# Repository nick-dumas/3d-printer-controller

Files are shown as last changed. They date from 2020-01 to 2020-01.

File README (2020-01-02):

This project is a 3D printer controller board.

The goals are (in the following order):
 * Safety (No electrical/fire hazards)
 * Print quality on par with the Duet
 * Modularity on par with ramps
 * Hobbiest level assembly difficulty
 * Cheap

It is intended to be used with a 24v LED strip switching PSU, as well as an external 5v buck-boost regulator.

Currently licensed under:
 Creative Commons Attribution-NonCommercial-ShareAlike 4.0 International License
 http://creativecommons.org/licenses/by-nc-sa/4.0/

This means share-alike, non-commercial.
I plan to release this under a open MIT license once the project is built and complete.
I would also appreciate if you let me know if and how you are using this project.

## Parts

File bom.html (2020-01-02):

Ref | Qnty | Value | Part | Footprint | Description | Vendor
A1, A2, A3, A4 | 4 | A9488_BREAKOUT | 3d-printer-controller:Pololu_Breakout_A4988 | Module:Pololu_Breakout-16_15.2x20.3mm | Pololu Breakout Board, Stepper Driver A4988
C1, C2, C4, C6, C7, C8, C9 | 7 | 1u | 3d-printer-controller:C | Capacitor_THT:C_Disc_D7.5mm_W2.5mm_P5.00mm | Unpolarized capacitor
C3, C5, C14, C15 | 4 | 10u | 3d-printer-controller:CP | Capacitor_THT:CP_Radial_D8.0mm_P5.00mm | Polarized capacitor
C10, C11, C12, C13 | 4 | 100u | 3d-printer-controller:CP | Capacitor_THT:CP_Radial_D10.0mm_P5.00mm | Polarized capacitor
C16 | 1 | C | 3d-printer-controller:C | Capacitor_THT:CP_Radial_D8.0mm_P5.00mm | Unpolarized capacitor
D1, D2 | 2 | D_Schottky | 3d-printer-controller:D_Schottky | Diode_THT:D_A-405_P10.16mm_Horizontal | Schottky diode
F1 | 1 | FUSE_FAN_1A | 3d-printer-controller:Fuse | Fuse:Fuseholder_Blade_Mini_Keystone_3568 | Fuse
F2 | 1 | FUSE_HEAT_15A | 3d-printer-controller:Fuse | Fuse:Fuseholder_Blade_Mini_Keystone_3568 | Fuse
F3 | 1 | FUSE_MOT_10A | 3d-printer-controller:Fuse | Fuse:Fuseholder_Blade_Mini_Keystone_3568 | Fuse
J1 | 1 | X_MIN | 3d-printer-controller:Conn_01x03 | Connector_PinHeader_2.54mm:PinHeader_1x03_P2.54mm_Vertical | Generic connector, single row, 01x03, script generated (kicad-library-utils/schlib/autogen/connector/)
J2 | 1 | X_MAX | 3d-printer-controller:Conn_01x03 | Connector_PinHeader_2.54mm:PinHeader_1x03_P2.54mm_Vertical | Generic connector, single row, 01x03, script generated (kicad-library-utils/schlib/autogen/connector/)
J3, J5 | 2 | THRM0 | 3d-printer-controller:Conn_01x02 | Connector_PinHeader_2.54mm:PinHeader_2x01_P2.54mm_Vertical | Generic connector, single row, 01x02, script generated (kicad-library-utils/schlib/autogen/connector/)
J4 | 1 | Y_MIN | 3d-printer-controller:Conn_01x03 | Connector_PinHeader_2.54mm:PinHeader_1x03_P2.54mm_Vertical | Generic connector, single row, 01x03, script generated (kicad-library-utils/schlib/autogen/connector/)
J6 | 1 | Y_MAX | 3d-printer-controller:Conn_01x03 | Connector_PinHeader_2.54mm:PinHeader_1x03_P2.54mm_Vertical | Generic connector, single row, 01x03, script generated (kicad-library-utils/schlib/autogen/connector/)
J7 | 1 | Z_MIN | 3d-printer-controller:Conn_01x03 | Connector_PinHeader_2.54mm:PinHeader_1x03_P2.54mm_Vertical | Generic connector, single row, 01x03, script generated (kicad-library-utils/schlib/autogen/connector/)
J8 | 1 | Z_MAX | 3d-printer-controller:Conn_01x03 | Connector_PinHeader_2.54mm:PinHeader_1x03_P2.54mm_Vertical | Generic connector, single row, 01x03, script generated (kicad-library-utils/schlib/autogen/connector/)
J9 | 1 | MICROUSB | 3d-printer-controller:USB_B_Micro | Connector_USB:USB_Micro-B_Molex_47346-0001 | USB Micro Type B connector
J10 | 1 | I2C | 3d-printer-controller:Conn_01x04 | Connector_PinHeader_2.54mm:PinHeader_1x04_P2.54mm_Vertical | Generic connector, single row, 01x04, script generated (kicad-library-utils/schlib/autogen/connector/)
J11 | 1 | SD_Card | 3d-printer-controller:SD_Card | Connector_Card:SD_TE_2041021 | SD Card Reader
J12 | 1 | Z_MOT_JMP | 3d-printer-controller:Conn_02x03_Top_Bottom | Connector_PinHeader_2.54mm:PinHeader_2x03_P2.54mm_Vertical | Generic connector, double row, 02x03, top/bottom pin numbering scheme (row 1: 1...pins_per_row, row2: pins_per_row+1 ... num_pins), script generated (kicad-library-utils/schlib/autogen/connector/)
J13 | 1 | X_MOT_JMP | 3d-printer-controller:Conn_02x03_Top_Bottom | Connector_PinHeader_2.54mm:PinHeader_2x03_P2.54mm_Vertical | Generic connector, double row, 02x03, top/bottom pin numbering scheme (row 1: 1...pins_per_row, row2: pins_per_row+1 ... num_pins), script generated (kicad-library-utils/schlib/autogen/connector/)
J14 | 1 | Z_MOT | 3d-printer-controller:Conn_01x04 | Connector_PinHeader_2.54mm:PinHeader_1x04_P2.54mm_Vertical | Generic connector, single row, 01x04, script generated (kicad-library-utils/schlib/autogen/connector/)
J15 | 1 | X_MOT | 3d-printer-controller:Conn_01x04 | Connector_PinHeader_2.54mm:PinHeader_1x04_P2.54mm_Vertical | Generic connector, single row, 01x04, script generated (kicad-library-utils/schlib/autogen/connector/)
J16 | 1 | E0_MOT_JMP | 3d-printer-controller:Conn_02x03_Top_Bottom | Connector_PinHeader_2.54mm:PinHeader_2x03_P2.54mm_Vertical | Generic connector, double row, 02x03, top/bottom pin numbering scheme (row 1: 1...pins_per_row, row2: pins_per_row+1 ... num_pins), script generated (kicad-library-utils/schlib/autogen/connector/)
J17 | 1 | Y_MOT_JMP | 3d-printer-controller:Conn_02x03_Top_Bottom | Connector_PinHeader_2.54mm:PinHeader_2x03_P2.54mm_Vertical | Generic connector, double row, 02x03, top/bottom pin numbering scheme (row 1: 1...pins_per_row, row2: pins_per_row+1 ... num_pins), script generated (kicad-library-utils/schlib/autogen/connector/)
J18 | 1 | E0_MOT | 3d-printer-controller:Conn_01x04 | Connector_PinHeader_2.54mm:PinHeader_1x04_P2.54mm_Vertical | Generic connector, single row, 01x04, script generated (kicad-library-utils/schlib/autogen/connector/)
J19 | 1 | Y_MOT | 3d-printer-controller:Conn_01x04 | Connector_PinHeader_2.54mm:PinHeader_1x04_P2.54mm_Vertical | Generic connector, single row, 01x04, script generated (kicad-library-utils/schlib/autogen/connector/)
J20 | 1 | FAN1 | 3d-printer-controller:Conn_01x02 | Connector_PinHeader_2.54mm:PinHeader_1x02_P2.54mm_Vertical | Generic connector, single row, 01x02, script generated (kicad-library-utils/schlib/autogen/connector/)
J21 | 1 | FAN0 | 3d-printer-controller:Conn_01x02 | Connector_PinHeader_2.54mm:PinHeader_1x02_P2.54mm_Vertical | Generic connector, single row, 01x02, script generated (kicad-library-utils/schlib/autogen/connector/)
J22 | 1 | HEAT1 | 3d-printer-controller:Conn_01x02 | Connector_PinHeader_2.54mm:PinHeader_1x02_P2.54mm_Vertical | Generic connector, single row, 01x02, script generated (kicad-library-utils/schlib/autogen/connector/)
J23 | 1 | HEAT0 | 3d-printer-controller:Conn_01x02 | Connector_PinHeader_2.54mm:PinHeader_1x02_P2.54mm_Vertical | Generic connector, single row, 01x02, script generated (kicad-library-utils/schlib/autogen/connector/)
J24 | 1 | FAN_PWR | 3d-printer-controller:Screw_Terminal_01x02 | TerminalBlock:TerminalBlock_Altech_AK300-2_P5.00mm | Generic screw terminal, single row, 01x02, script generated (kicad-library-utils/schlib/autogen/connector/)
J25 | 1 | HEAT_PWR | 3d-printer-controller:Screw_Terminal_01x02 | TerminalBlock:TerminalBlock_Altech_AK300-2_P5.00mm | Generic screw terminal, single row, 01x02, script generated (kicad-library-utils/schlib/autogen/connector/)
J26 | 1 | MOT_PWR | 3d-printer-controller:Screw_Terminal_01x02 | TerminalBlock:TerminalBlock_Altech_AK300-2_P5.00mm | Generic screw terminal, single row, 01x02, script generated (kicad-library-utils/schlib/autogen/connector/)
J27 | 1 | VIN | 3d-printer-controller:Screw_Terminal_01x02 | TerminalBlock:TerminalBlock_Altech_AK300-2_P5.00mm | Generic screw terminal, single row, 01x02, script generated (kicad-library-utils/schlib/autogen/connector/)
Q1, Q2, Q3, Q4 | 4 | IRFB7546PBF | 3d-printer-controller:IRFB7546PBF | Package_TO_SOT_THT:TO-220-3_Vertical | MOSFET N CH 60V 75A TO-220AB
R1, R2, R4, R6, R7, R8, R12, R13, R14, R15, R28 | 11 | 10k | 3d-printer-controller:R | Resistor_THT:R_Axial_DIN0207_L6.3mm_D2.5mm_P10.16mm_Horizontal | Resistor
R3, R5, R10, R11 | 4 | 4.7k | 3d-printer-controller:R | Resistor_THT:R_Axial_DIN0207_L6.3mm_D2.5mm_P10.16mm_Horizontal | Resistor
R9 | 1 | 1.5k | 3d-printer-controller:R | Resistor_THT:R_Axial_DIN0207_L6.3mm_D2.5mm_P10.16mm_Horizontal | Resistor
R16, R17, R23 | 3 | 560 | 3d-printer-controller:R | Resistor_THT:R_Axial_DIN0207_L6.3mm_D2.5mm_P10.16mm_Horizontal | Resistor
R18, R19, R22, R24, R25 | 5 | 1k | 3d-printer-controller:R | Resistor_THT:R_Axial_DIN0207_L6.3mm_D2.5mm_P10.16mm_Horizontal | Resistor
R20, R21, R26, R27 | 4 | 270 | 3d-printer-controller:R | Resistor_THT:R_Axial_DIN0207_L6.3mm_D2.5mm_P10.16mm_Horizontal | Resistor
SW1 | 1 | SW_RST | 3d-printer-controller:SW_Push | Button_Switch_THT:SW_PUSH_6mm_H5mm | Push button switch, generic, two pins
U1 | 1 | STM32F103C8_Breakout | 3d-printer-controller:STM32F103C8_Breakout | 3d-printer-controller:DIP-40_600_ELL | Dev board for small STM microcontroller. AKA blue pill.
U2, U3, U4, U5 | 4 | TPC817B_C9G | 3d-printer-controller:TPC817B_C9G | Package_DIP:DIP-4_W7.62mm_Socket | Optocoupler, LED Input, Photocell Output
U6 | 1 | MC33269T-3.3G | 3d-printer-controller:MC33269T-3.3G | Package_TO_SOT_THT:TO-220-3_Vertical | LDO Voltage Regulators 3.3V ADJ 800mA

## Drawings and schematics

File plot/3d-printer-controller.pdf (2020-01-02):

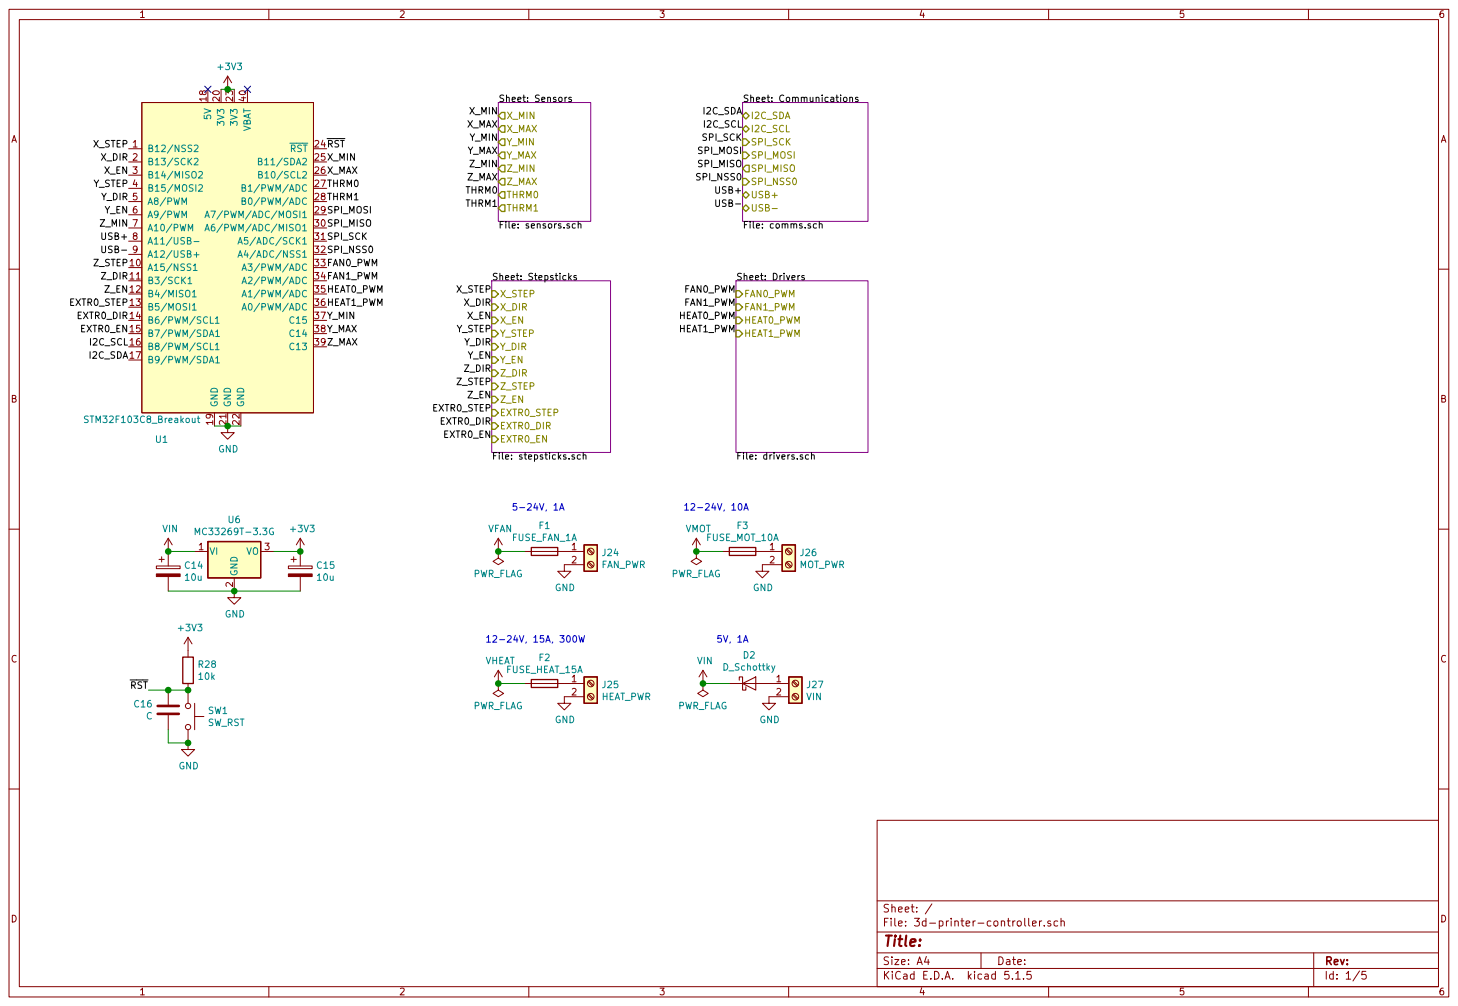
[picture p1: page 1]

SPI_MISO
Sheet: Drivers File: drivers.sch FAN0_PWM

File: 3d-printer-controller.sch Sheet: /
Id: 1/5 Title:

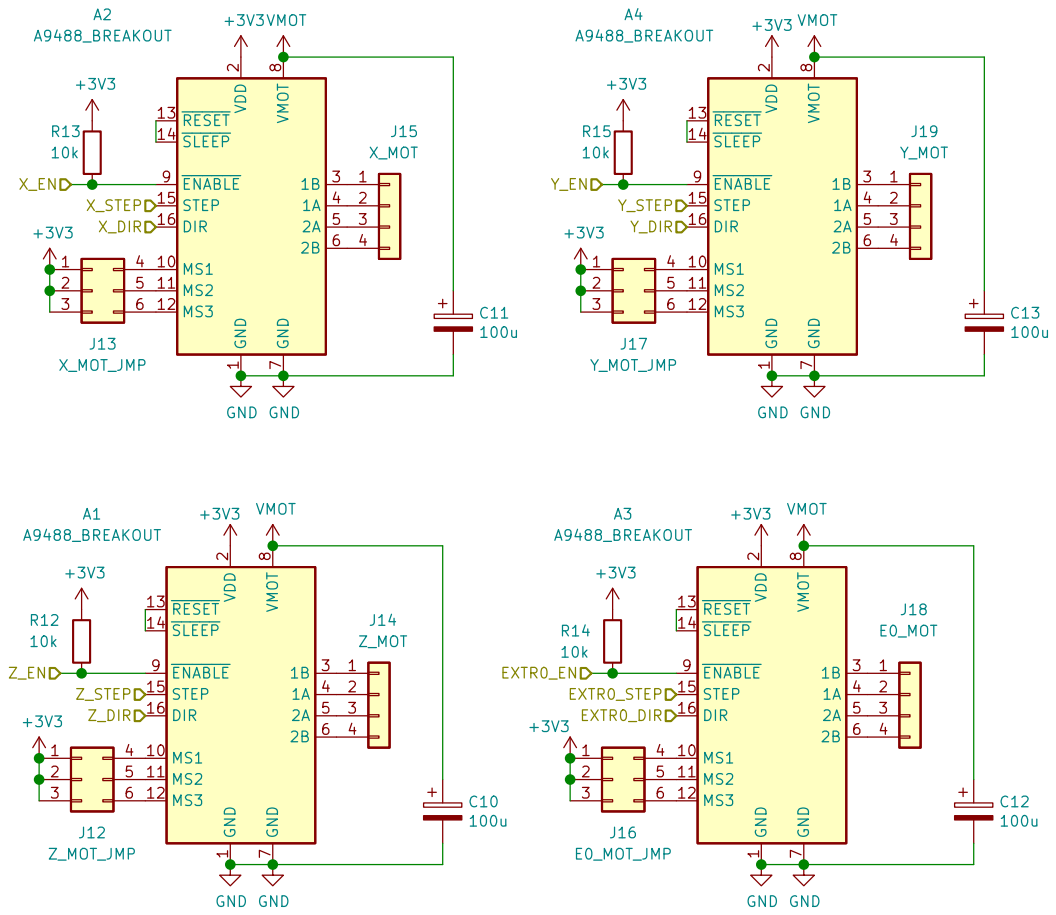
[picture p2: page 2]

1 MS1 10 MS2 11 MS3 12 RESET 13 SLEEP 14 STEP 15 DIR 16 VDD

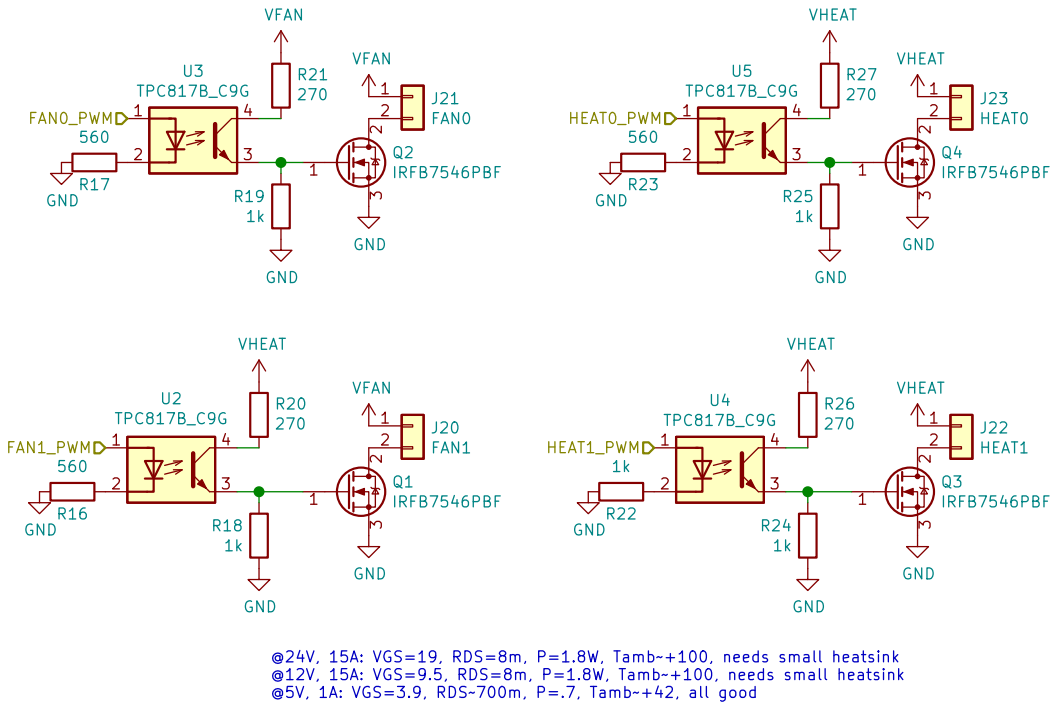
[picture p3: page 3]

Id: 3/5 Title: File: drivers.sch Sheet: /Drivers/ R24

@12V, 15A: VGS=9.5, RDS=8m, P=1.8W, Tamb+100, needs small heatsink
@5V, 1A: VGS=3.9, RDS700m, P=.7, Tamb+42, all good

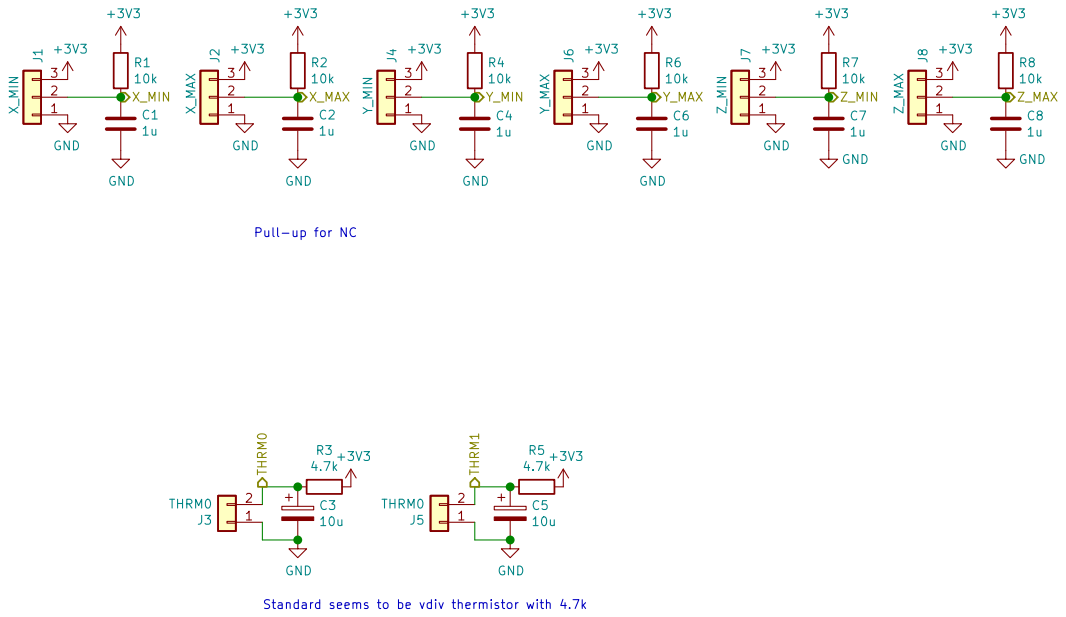
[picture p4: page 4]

Pull-up for NC

Standard seems to be vdiv thermistor with 4.7k

Id: 4/5 Title: File: sensors.sch Sheet: /Sensors/

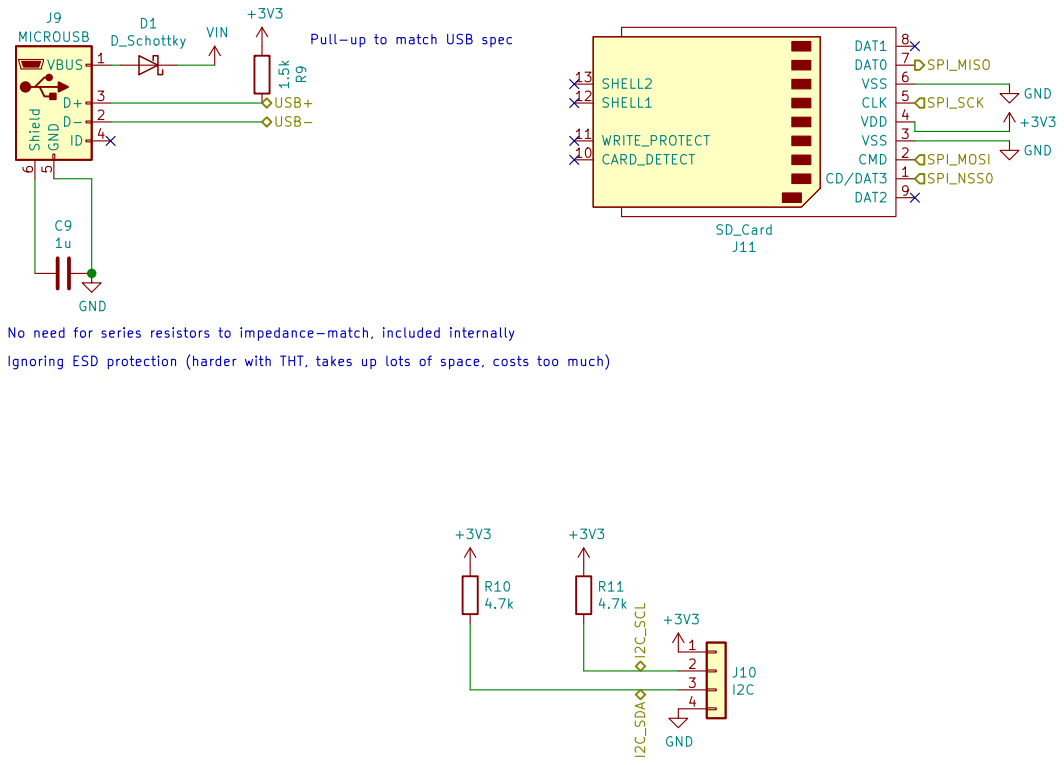
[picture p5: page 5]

SPI_MOSI SPI_NSS0 Pull-up to match USB spec

No need for series resistors to impedance-match, included internally
Ignoring ESD protection (harder with THT, takes up lots of space, costs too much)

Id: 5/5 Title: File: comms.sch Sheet: /Communications/

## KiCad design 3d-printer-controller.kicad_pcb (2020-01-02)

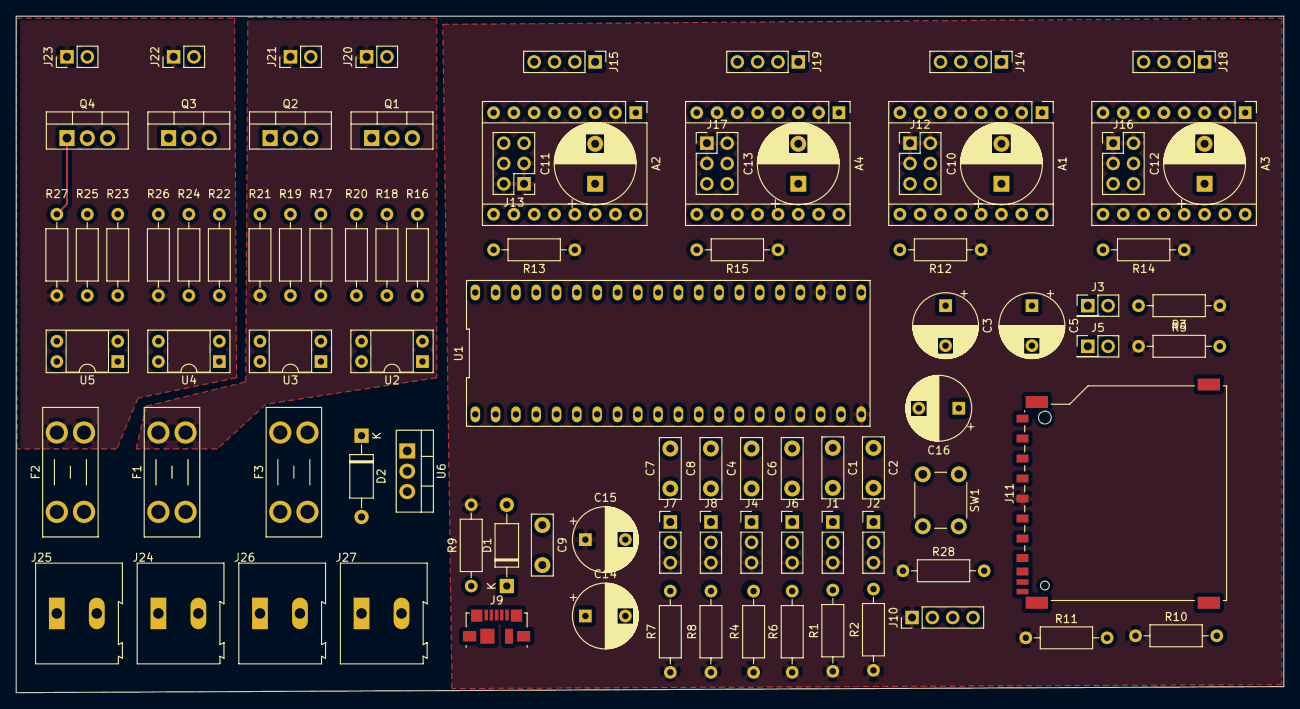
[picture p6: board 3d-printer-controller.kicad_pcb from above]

Board: 2 copper layers, 158.5 x 84.6 mm, 91 parts (0 on the bottom side), 93 nets.

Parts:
A1, A2, A3, A4: A9488_BREAKOUT; Pololu_Breakout-16_15.2x20.3mm
C1, C2, C4, C6, C7, C8, C9: 1u; C_Disc_D7.5mm_W2.5mm_P5.00mm
C3, C5, C14, C15: 10u; CP_Radial_D8.0mm_P5.00mm
C10, C11, C12, C13: 100u; CP_Radial_D10.0mm_P5.00mm
C16: C; CP_Radial_D8.0mm_P5.00mm
D1, D2: D_Schottky; D_A-405_P10.16mm_Horizontal
F1: FUSE_FAN_1A; Fuseholder_Blade_Mini_Keystone_3568
F2: FUSE_HEAT_15A; Fuseholder_Blade_Mini_Keystone_3568
F3: FUSE_MOT_10A; Fuseholder_Blade_Mini_Keystone_3568
J1: X_MIN; PinHeader_1x03_P2.54mm_Vertical
J2: X_MAX; PinHeader_1x03_P2.54mm_Vertical
J3, J5: THRM0; PinHeader_2x01_P2.54mm_Vertical
J4: Y_MIN; PinHeader_1x03_P2.54mm_Vertical
J6: Y_MAX; PinHeader_1x03_P2.54mm_Vertical
J7: Z_MIN; PinHeader_1x03_P2.54mm_Vertical
J8: Z_MAX; PinHeader_1x03_P2.54mm_Vertical
J9: MICROUSB; USB_Micro-B_Molex_47346-0001
J10: I2C; PinHeader_1x04_P2.54mm_Vertical
J11: SD_Card; SD_TE_2041021
J12: Z_MOT_JMP; PinHeader_2x03_P2.54mm_Vertical
J13: X_MOT_JMP; PinHeader_2x03_P2.54mm_Vertical
J14: Z_MOT; PinHeader_1x04_P2.54mm_Vertical
J15: X_MOT; PinHeader_1x04_P2.54mm_Vertical
J16: E0_MOT_JMP; PinHeader_2x03_P2.54mm_Vertical
J17: Y_MOT_JMP; PinHeader_2x03_P2.54mm_Vertical
J18: E0_MOT; PinHeader_1x04_P2.54mm_Vertical
J19: Y_MOT; PinHeader_1x04_P2.54mm_Vertical
J20: FAN1; PinHeader_1x02_P2.54mm_Vertical
J21: FAN0; PinHeader_1x02_P2.54mm_Vertical
J22: HEAT1; PinHeader_1x02_P2.54mm_Vertical
J23: HEAT0; PinHeader_1x02_P2.54mm_Vertical
J24: FAN_PWR; TerminalBlock_Altech_AK300-2_P5.00mm
J25: HEAT_PWR; TerminalBlock_Altech_AK300-2_P5.00mm
J26: MOT_PWR; TerminalBlock_Altech_AK300-2_P5.00mm
J27: VIN; TerminalBlock_Altech_AK300-2_P5.00mm
Q1, Q2, Q3, Q4: IRFB7546PBF; TO-220-3_Vertical
R1, R2, R4, R6, R7, R8, R12, R13, R14, R15, R28: 10k; R_Axial_DIN0207_L6.3mm_D2.5mm_P10.16mm_Horizontal
R3, R5, R10, R11: 4.7k; R_Axial_DIN0207_L6.3mm_D2.5mm_P10.16mm_Horizontal
R9: 1.5k; R_Axial_DIN0207_L6.3mm_D2.5mm_P10.16mm_Horizontal
R16, R17, R23: 560; R_Axial_DIN0207_L6.3mm_D2.5mm_P10.16mm_Horizontal
R18, R19, R22, R24, R25: 1k; R_Axial_DIN0207_L6.3mm_D2.5mm_P10.16mm_Horizontal
R20, R21, R26, R27: 270; R_Axial_DIN0207_L6.3mm_D2.5mm_P10.16mm_Horizontal
SW1: SW_RST; SW_PUSH_6mm_H5mm
U1: blue_pill; DIP-40_600_ELL
U2, U3, U4, U5: TPC817B_C9G; DIP-4_W7.62mm_Socket
U6: MC33269T-3.3G; TO-220-3_Vertical

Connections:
+3V3: A1.2, A2.2, A3.2, A4.2, C15.1, J1.3, J2.3, J4.3, J6.3, J7.3, J8.3, J10.1, J11.4, J12.1, J12.2, J12.3, J13.1, J13.2, J13.3, J16.1, J16.2, J16.3, J17.1, J17.2, J17.3, R1.1, R2.1, R3.1, R4.1, R5.1, R6.1, R7.1, R8.1, R9.2, R10.1, R11.1, R12.1, R13.1, R14.1, R15.1, R28.1, U1.20, U1.23, U6.3
/EXTR0_DIR: A3.16, U1.14
/EXTR0_EN: A3.9, R14.2, U1.15
/EXTR0_STEP: A3.15, U1.13
/FAN0_PWM: U1.33, U3.1
/FAN1_PWM: U1.34, U2.1
/HEAT0_PWM: U1.35, U5.1
/HEAT1_PWM: U1.36, U4.1
/I2C_SCL: J10.2, R11.2, U1.16
/I2C_SDA: J10.3, R10.2, U1.17
/SPI_MISO: J11.7, U1.30
/SPI_MOSI: J11.2, U1.29
/SPI_NSS0: J11.1, U1.32
/SPI_SCK: J11.5, U1.31
/THRM0: C3.1, J3.2, R3.2, U1.27
/THRM1: C5.1, J5.2, R5.2, U1.28
/USB+: J9.3, R9.1, U1.8
/USB-: J9.2, U1.9
/X_DIR: A2.16, U1.2
/X_EN: A2.9, R13.2, U1.3
/X_MAX: C2.2, J2.2, R2.2, U1.26
/X_MIN: C1.2, J1.2, R1.2, U1.25
/X_STEP: A2.15, U1.1
/Y_DIR: A4.16, U1.5
/Y_EN: A4.9, R15.2, U1.6
/Y_MAX: C6.1, J6.2, R6.2, U1.38
/Y_MIN: C4.1, J4.2, R4.2, U1.37
/Y_STEP: A4.15, U1.4
/Z_DIR: A1.16, U1.11
/Z_EN: A1.9, R12.2, U1.12
/Z_MAX: C8.1, J8.2, R8.2, U1.39
/Z_MIN: C7.1, J7.2, R7.2, U1.7
/Z_STEP: A1.15, U1.10
/~RST: C16.1, R28.2, SW1.1, U1.24
GND: A1.1, A1.7, A2.1, A2.7, A3.1, A3.7, A4.1, A4.7, C1.1, C2.1, C3.2, C4.2, C5.2, C6.2, C7.2, C8.2, C9.1, C10.2, C11.2, C12.2, C13.2, C14.2, C15.2, C16.2, J1.1, J2.1, J3.1, J4.1, J5.1, J6.1, J7.1, J8.1, J9.5, J10.4, J11.3, J11.6, J24.2, J25.2, J26.2, J27.2, Q1.3, Q2.3, Q3.3, Q4.3, R16.2, R17.2, R18.2, R19.2, R22.2, R23.2, R24.2, R25.2, SW1.2, U1.19, U1.21, U1.22, U6.2
unnamed: A1.3, J14.1
unnamed: A1.4, J14.2
unnamed: A1.5, J14.3
unnamed: A1.6, J14.4
unnamed: A1.10, J12.4
unnamed: A1.11, J12.5
unnamed: A1.12, J12.6
unnamed: A1.13, A1.14
unnamed: A2.3, J15.1
unnamed: A2.4, J15.2
unnamed: A2.5, J15.3
unnamed: A2.6, J15.4
unnamed: A2.10, J13.4
unnamed: A2.11, J13.5
unnamed: A2.12, J13.6
unnamed: A2.13, A2.14
unnamed: A3.3, J18.1
unnamed: A3.4, J18.2
unnamed: A3.5, J18.3
unnamed: A3.6, J18.4
unnamed: A3.10, J16.4
unnamed: A3.11, J16.5
unnamed: A3.12, J16.6
unnamed: A3.13, A3.14
unnamed: A4.3, J19.1
unnamed: A4.4, J19.2
unnamed: A4.5, J19.3
unnamed: A4.6, J19.4
unnamed: A4.10, J17.4
unnamed: A4.11, J17.5
unnamed: A4.12, J17.6
unnamed: A4.13, A4.14
unnamed: C9.2, J9.6
unnamed: D1.2, J9.1
unnamed: D2.2, J27.1
unnamed: F1.1, J24.1
unnamed: F2.1, J25.1
unnamed: F3.1, J26.1
unnamed: J20.2, Q1.2
unnamed: J21.2, Q2.2
unnamed: J22.2, Q3.2
unnamed: J23.2, Q4.2
unnamed: Q1.1, R18.1, U2.3
unnamed: Q2.1, R19.1, U3.3
unnamed: Q3.1, R24.1, U4.3
unnamed: Q4.1, R25.1, U5.3
unnamed: R16.1, U2.2
unnamed: R17.1, U3.2
unnamed: R20.1, U2.4
unnamed: R21.1, U3.4
unnamed: R22.1, U4.2
unnamed: R23.1, U5.2
unnamed: R26.1, U4.4
unnamed: R27.1, U5.4
VFAN: F1.2, J20.1, J21.1, R21.2
VHEAT: F2.2, J22.1, J23.1, R20.2, R26.2, R27.2
VIN: C14.1, D1.1, D2.1, U6.1
VMOT: A1.8, A2.8, A3.8, A4.8, C10.1, C11.1, C12.1, C13.1, F3.2

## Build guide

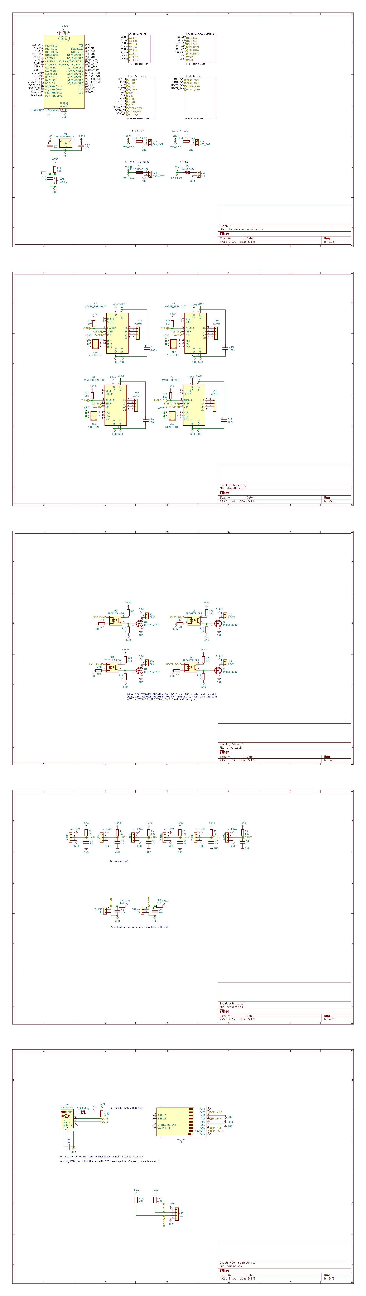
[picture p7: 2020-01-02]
plot/3d-printer-controller.jpg
